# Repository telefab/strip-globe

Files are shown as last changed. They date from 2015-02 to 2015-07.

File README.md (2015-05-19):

LED strip-based, FPGA-powered POV globe
===

Documentation
---

Documentation is [available on Instructables](http://www.instructables.com/id/Globe-of-persistence-of-vision/).

Source structure
---

* `app_sources`: sources of programs running on the globe
* `board`: power board Eagle model
* `fpga_sources`: VHDL files for the FPGA
* `Solidworks`: model for the physical design
* `zybo_project`: integration on the Zybo board. The Vivado project references the `fpga_sources` files

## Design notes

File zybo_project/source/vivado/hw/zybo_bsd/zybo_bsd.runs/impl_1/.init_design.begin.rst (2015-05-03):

<?xml version="1.0"?>
<ProcessHandle Version="1" Minor="0">
    <Process Command=".planAhead." Owner="phhorrei" Host="" Pid="14742">
    </Process>
</ProcessHandle>

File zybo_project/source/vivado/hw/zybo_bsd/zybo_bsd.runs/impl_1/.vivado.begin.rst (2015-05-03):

<?xml version="1.0"?>
<ProcessHandle Version="1" Minor="0">
    <Process Command="vivado" Owner="phhorrei" Host="njord" Pid="14716">
    </Process>
</ProcessHandle>

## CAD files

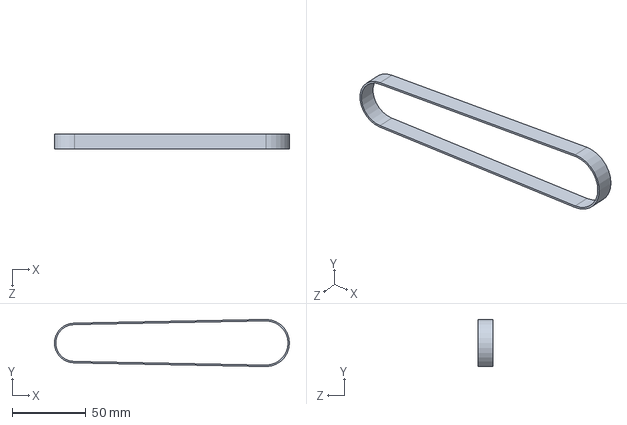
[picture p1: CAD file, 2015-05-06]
mechanics/courroie.SLDPRT
159.4 x 32.0 x 10.0 mm

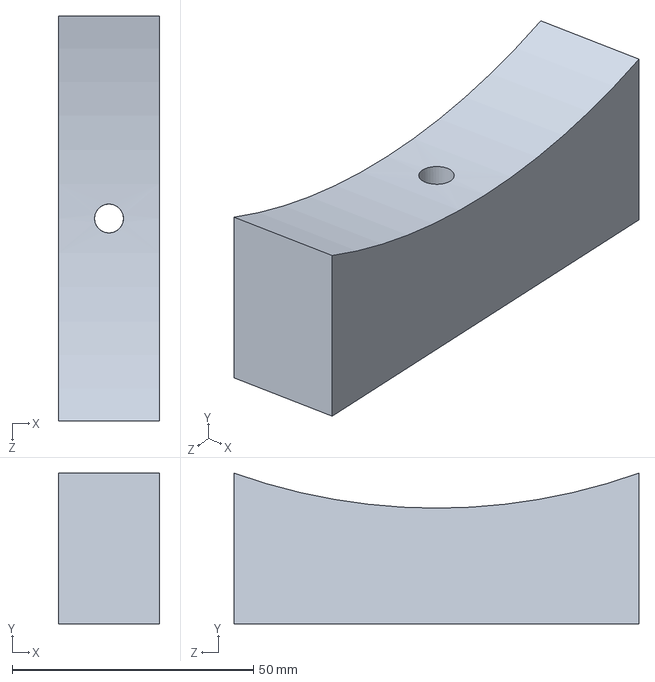
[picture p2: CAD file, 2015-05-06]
mechanics/Modélisation_anneau_fine/fixation_anneau.SLDPRT
21.0 x 31.3 x 84.0 mm

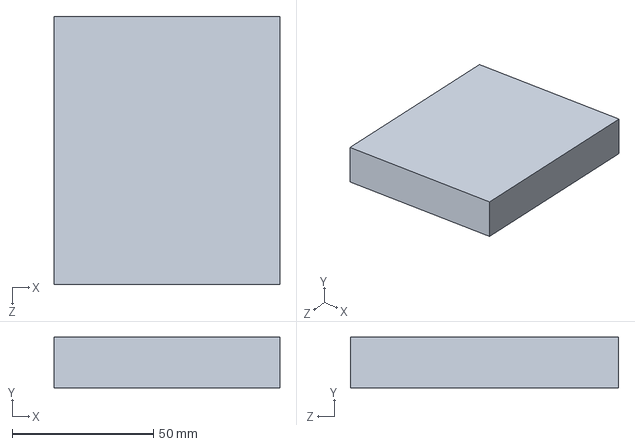
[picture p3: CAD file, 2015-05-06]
mechanics/Modélisation_structure_moteur/toit_structure.SLDPRT
80.0 x 18.0 x 95.0 mm

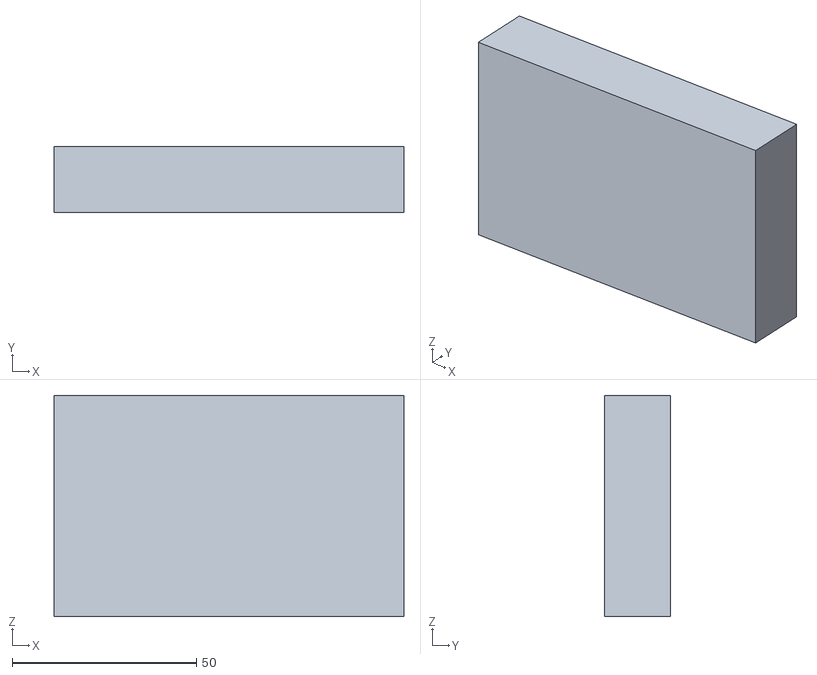
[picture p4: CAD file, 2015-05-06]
mechanics/STL/liaison_structure_moteur.STL
95.0 x 18.0 x 60.0

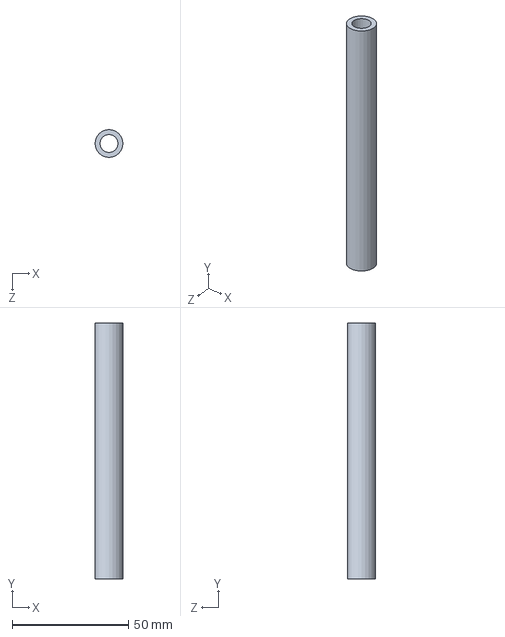
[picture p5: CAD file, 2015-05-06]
mechanics/axe_creux.SLDPRT
12.0 x 110.0 x 12.0 mm

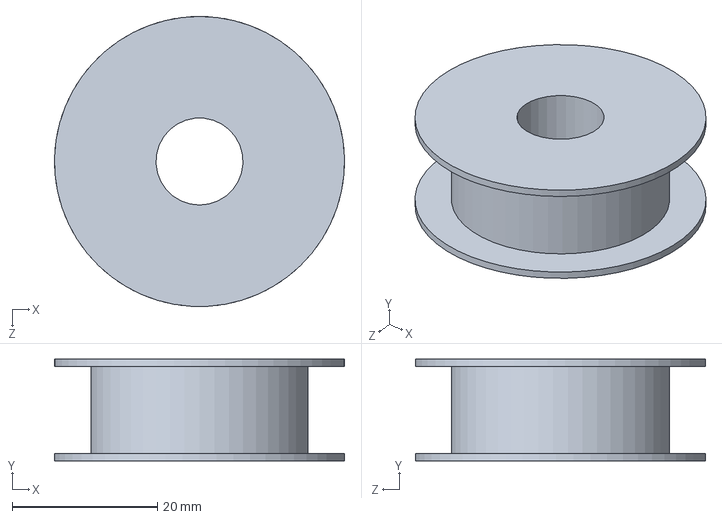
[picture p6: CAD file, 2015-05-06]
mechanics/Modélisation_anneau_fine/pignon_axe.SLDPRT
40.0 x 14.0 x 40.0 mm

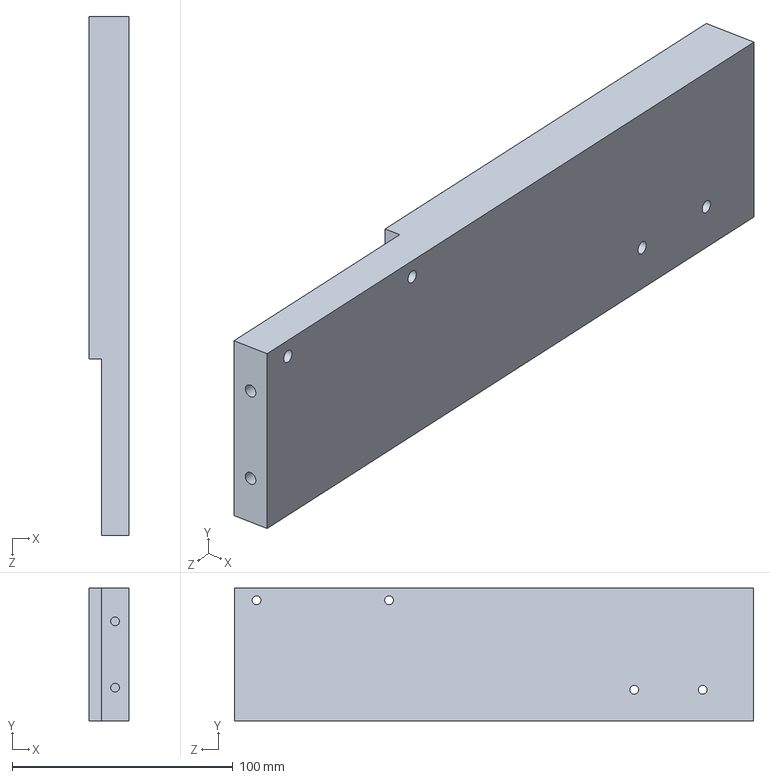
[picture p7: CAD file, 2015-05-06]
mechanics/Modélisation_structure_moteur/support_structure_moteur_sym.SLDPRT
18.0 x 60.0 x 235.0 mm

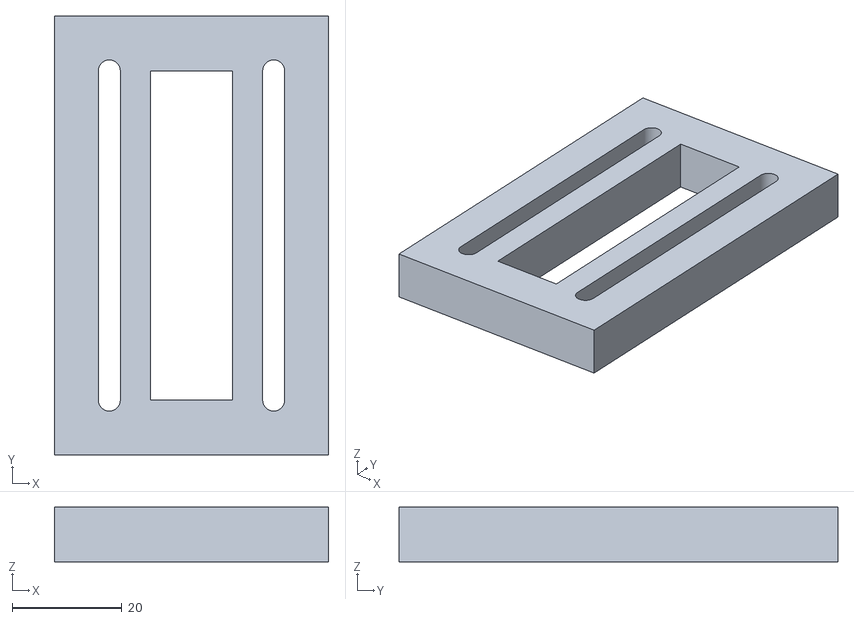
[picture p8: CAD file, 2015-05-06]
mechanics/STL/fixation_moteur_roof.STL
50.0 x 80.0 x 10.0

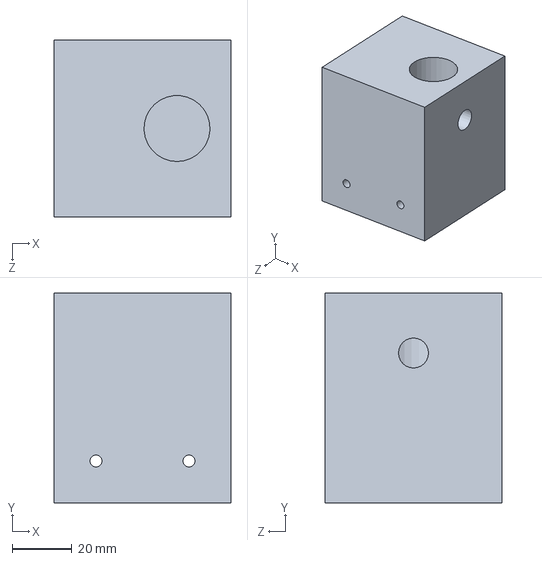
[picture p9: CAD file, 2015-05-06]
mechanics/Modélisation_anneau_fine/base.SLDPRT
59.0 x 70.0 x 59.0 mm

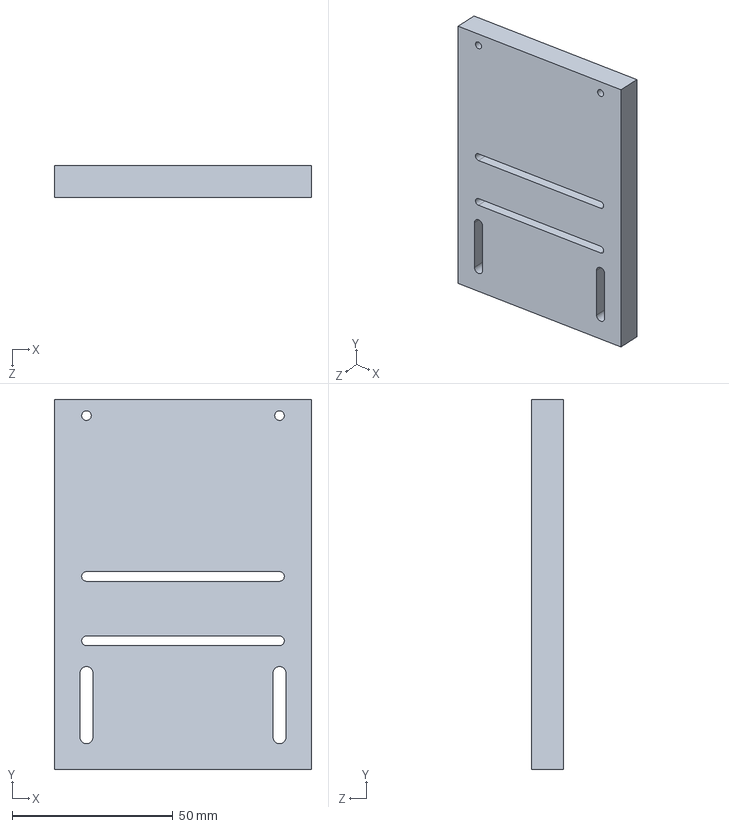
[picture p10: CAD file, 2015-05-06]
mechanics/Modélisation_structure_moteur/fixation_moteur_v2_side.SLDPRT
80.0 x 115.0 x 10.0 mm

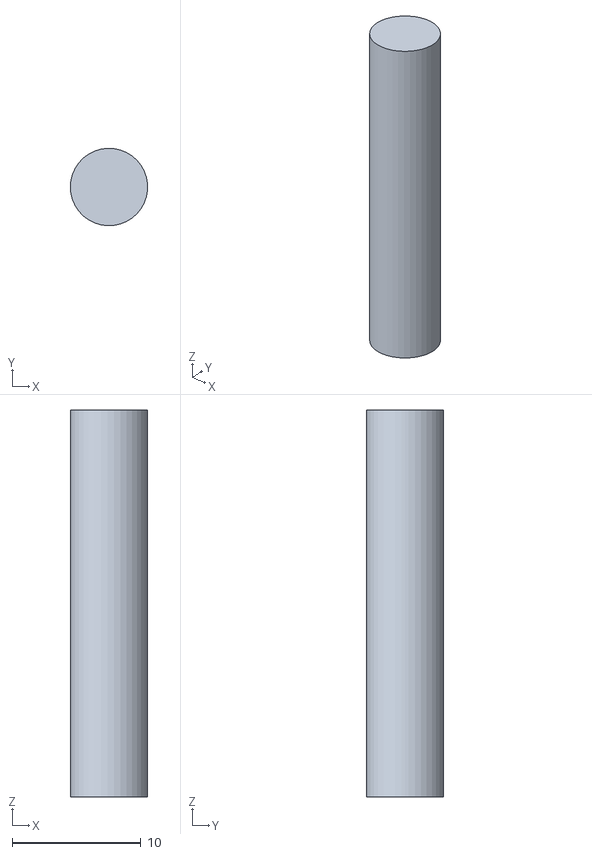
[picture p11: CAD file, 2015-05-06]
mechanics/STL/axe_soutien.STL
6.00 x 5.99 x 30.0

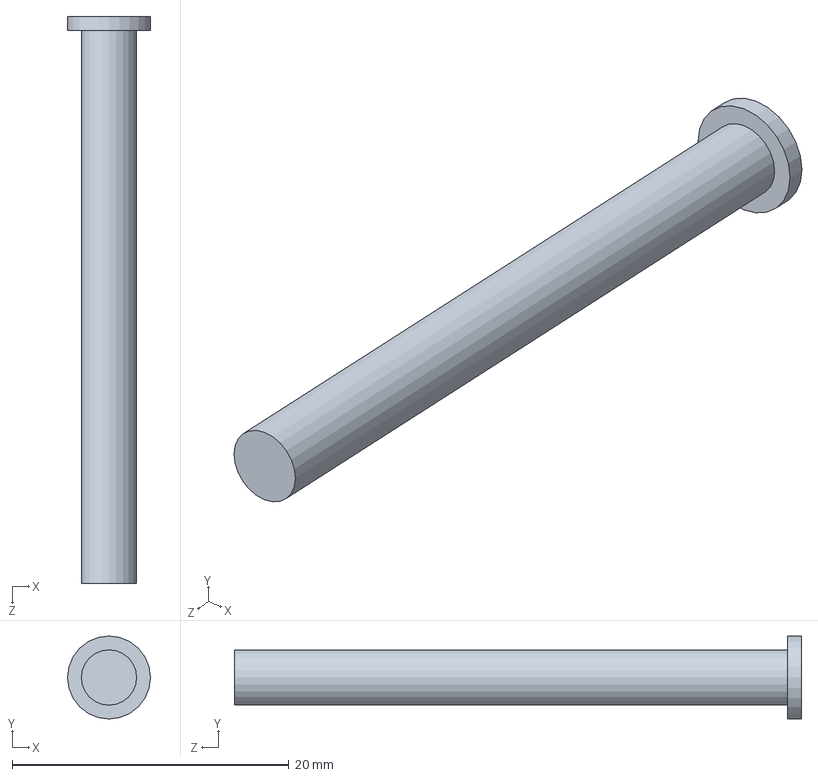
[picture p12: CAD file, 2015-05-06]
mechanics/vis_4.SLDPRT
6.00 x 6.00 x 41.0 mm

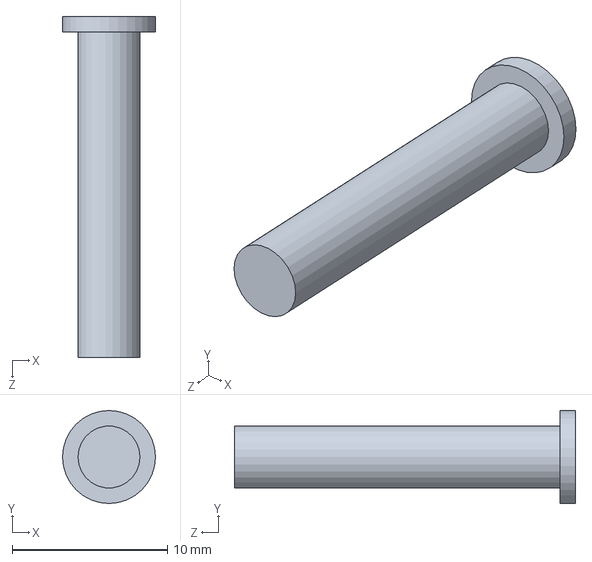
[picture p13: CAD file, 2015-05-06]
mechanics/mini_vis_4.SLDPRT
6.00 x 6.00 x 22.0 mm

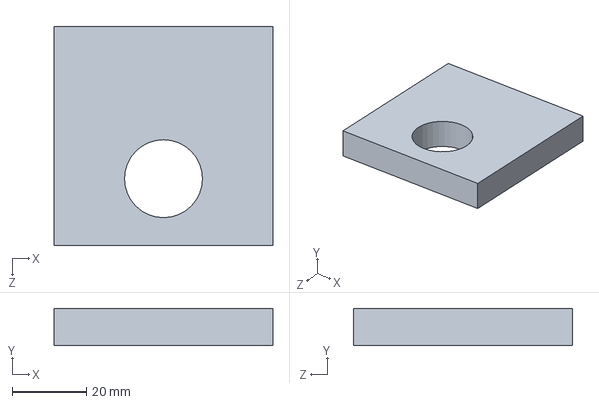
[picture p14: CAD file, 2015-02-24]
mechanics/Modélisation_anneau_fine/plaque.SLDPRT
59.0 x 10.0 x 59.0 mm

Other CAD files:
mechanics/Modélisation_structure_moteur/fixation_moteur_v2_roulement.SLDPRT
mechanics/STL/fixation_moteur_v2_side.STL
mechanics/Modélisation_anneau_fine/colonne.SLDPRT
mechanics/Modélisation_structure_moteur/fixation_moteur_roof.SLDPRT
mechanics/Modélisation_structure_moteur/axe_soutien.SLDPRT
mechanics/Modélisation_structure_moteur/fixation_moteur_v2.SLDPRT
mechanics/Modélisation_structure_moteur/liaison_structure_moteur.SLDPRT
mechanics/Modélisation_structure_moteur/moteur.SLDPRT
mechanics/Modélisation_structure_moteur/pignon_moteur_v2.SLDPRT
mechanics/Modélisation_structure_moteur/roulement_soutien_moteur.SLDPRT
mechanics/Modélisation_structure_moteur/support_globe.SLDPRT
mechanics/Modélisation_structure_moteur/support_structure_moteur.SLDPRT
mechanics/STL/anneau.STL
mechanics/STL/axe_creux.STL
mechanics/STL/base.STL
mechanics/STL/colonne.STL
mechanics/STL/fixation_anneau.STL
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

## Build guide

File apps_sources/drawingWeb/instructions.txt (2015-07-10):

// TODO: trouver un moyen de corriger définitivement les problèmes de permissions dans le dossier /var/www (devrait appartenir en entier à www-data) -> cause des 403 forbidden
// TODO 2: générer une clef rsa pour le serveur ssh. (http://www.softec.lu/site/DevelopersCorner/HowToRegenerateNewSsh ?)

1. Suivre l'instructable jusqu'à l'étape l'étape du buildroot:
  http://www.instructables.com/id/Globe-of-persistence-of-vision/step3/Installing-Linux-on-the-globe/

2. Installer lighttpd :
    make menuconfig
        target Package
                |
                ----> Networking Applications
                                |
                                -----> lighttpd
    sauvgarder/quitter
    
    make

3. Cross-compilation de node.js
    git clone 
    /!\ python doit être un lien vers python2
        Pour ceux dont ce n'est pas le cas -> ln -s /path/to/python2 python
                                              ln -s /path/to/python2-config python-config
                                              export PATH=`pwd`:$PATH
    export XILINX_TGT=arm-xilinx-linux-gnueabi
    export AR=$XILINX_TGT-ar
    export CC=$XILINX_TGT-gcc
    export CXX=$XILINX_TGT-g++
    export LINK=$XILINX_TGT-g++
    export PATH=$PATH:/path/to/xilinxToolchain/bin

    ./configure --without-snapshot --dest-cpu=arm --dest-os=linux

    make -j`nproc`
    make install DESTDIR=/dir/to/buildroot/output/target
    
    Copier libstdc+.so.6 du cross compilo dans /dir/to/buildroot/output/target/lib
    Personnelement j'ai trouvé libstdc++.so.6 dans
         /path/to/xilinxToolchain/libc/usr/lib/libstdc++.so.6

4. Compilation des modules node.js 
    avec les mêmes export que si dessus
            
    dans un répertoire choisi:
    pour chaque module :
        npm install nomDuModule --prefix=./ --target=arm

    mv node_modules /dir/to/buildroot/output/target/root

5. Finalistation
    dans le répertoire de buildroot :
    copier le contenu du dossier client dans le répertoire output/target/var/www
    copier le contenu du dossier server dans le répertoire output/target/root/sphereWeb-server
    make
    puis copier le output/images/rootfs.cpio.uboot sur la partition 1 de la microSD du globe et le renomer en uramdisk.image.gz

    Dans la partition 2 de la microSD:
        modifier le fichier load.sh pour démarrer le serveur nodejs et le logiciel du globe
        ajouter :

# Fix permissions on /var/www
chown www-data:www-data -R /var/www

## Start servers

cd /mnt
nohup /usr/local/bin/node /root/sphereWeb-server/server.js &
./drawing

    démonter la carte SD, rebooter le globe, tout devrait fonctionner

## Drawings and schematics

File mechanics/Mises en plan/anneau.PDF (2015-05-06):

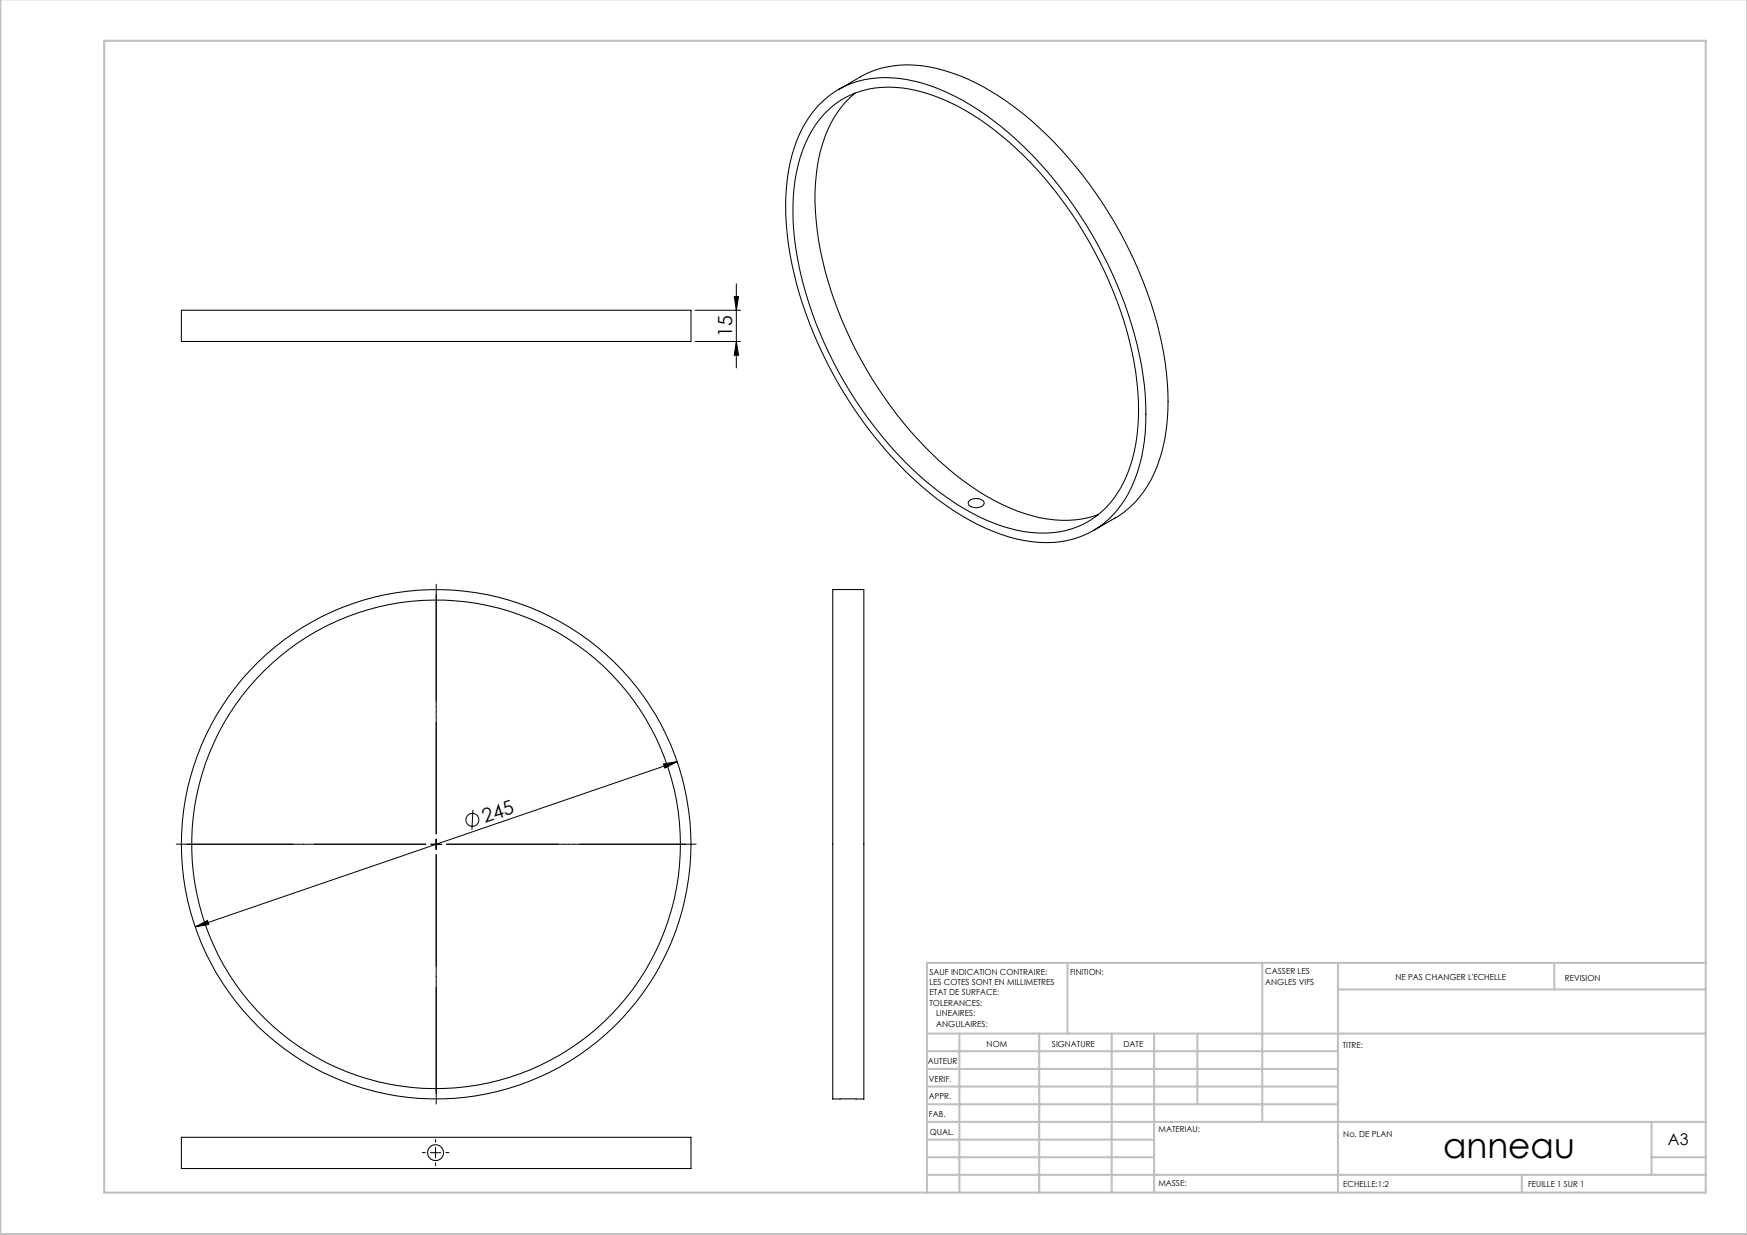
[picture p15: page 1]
ECHELLE:1:2; FEUILLE 1 SUR 1; NE PAS CHANGER L'ECHELLE; REVISION; CASSER LES ANGLES VIFS; SAUF INDICATION CONTRAIRE:; FINITION:

LES COTES SONT EN MILLIMETRES
ETAT DE SURFACE:
TOLERANCES:
LINEAIRES:
ANGULAIRES:

NOM | SIGNATURE | DATE | | | | TITRE:
QUAL. | | | | MATERIAU: | anneau MASSE: No. DE PLAN | A3

AUTEUR
VERIF.
APPR.
FAB.

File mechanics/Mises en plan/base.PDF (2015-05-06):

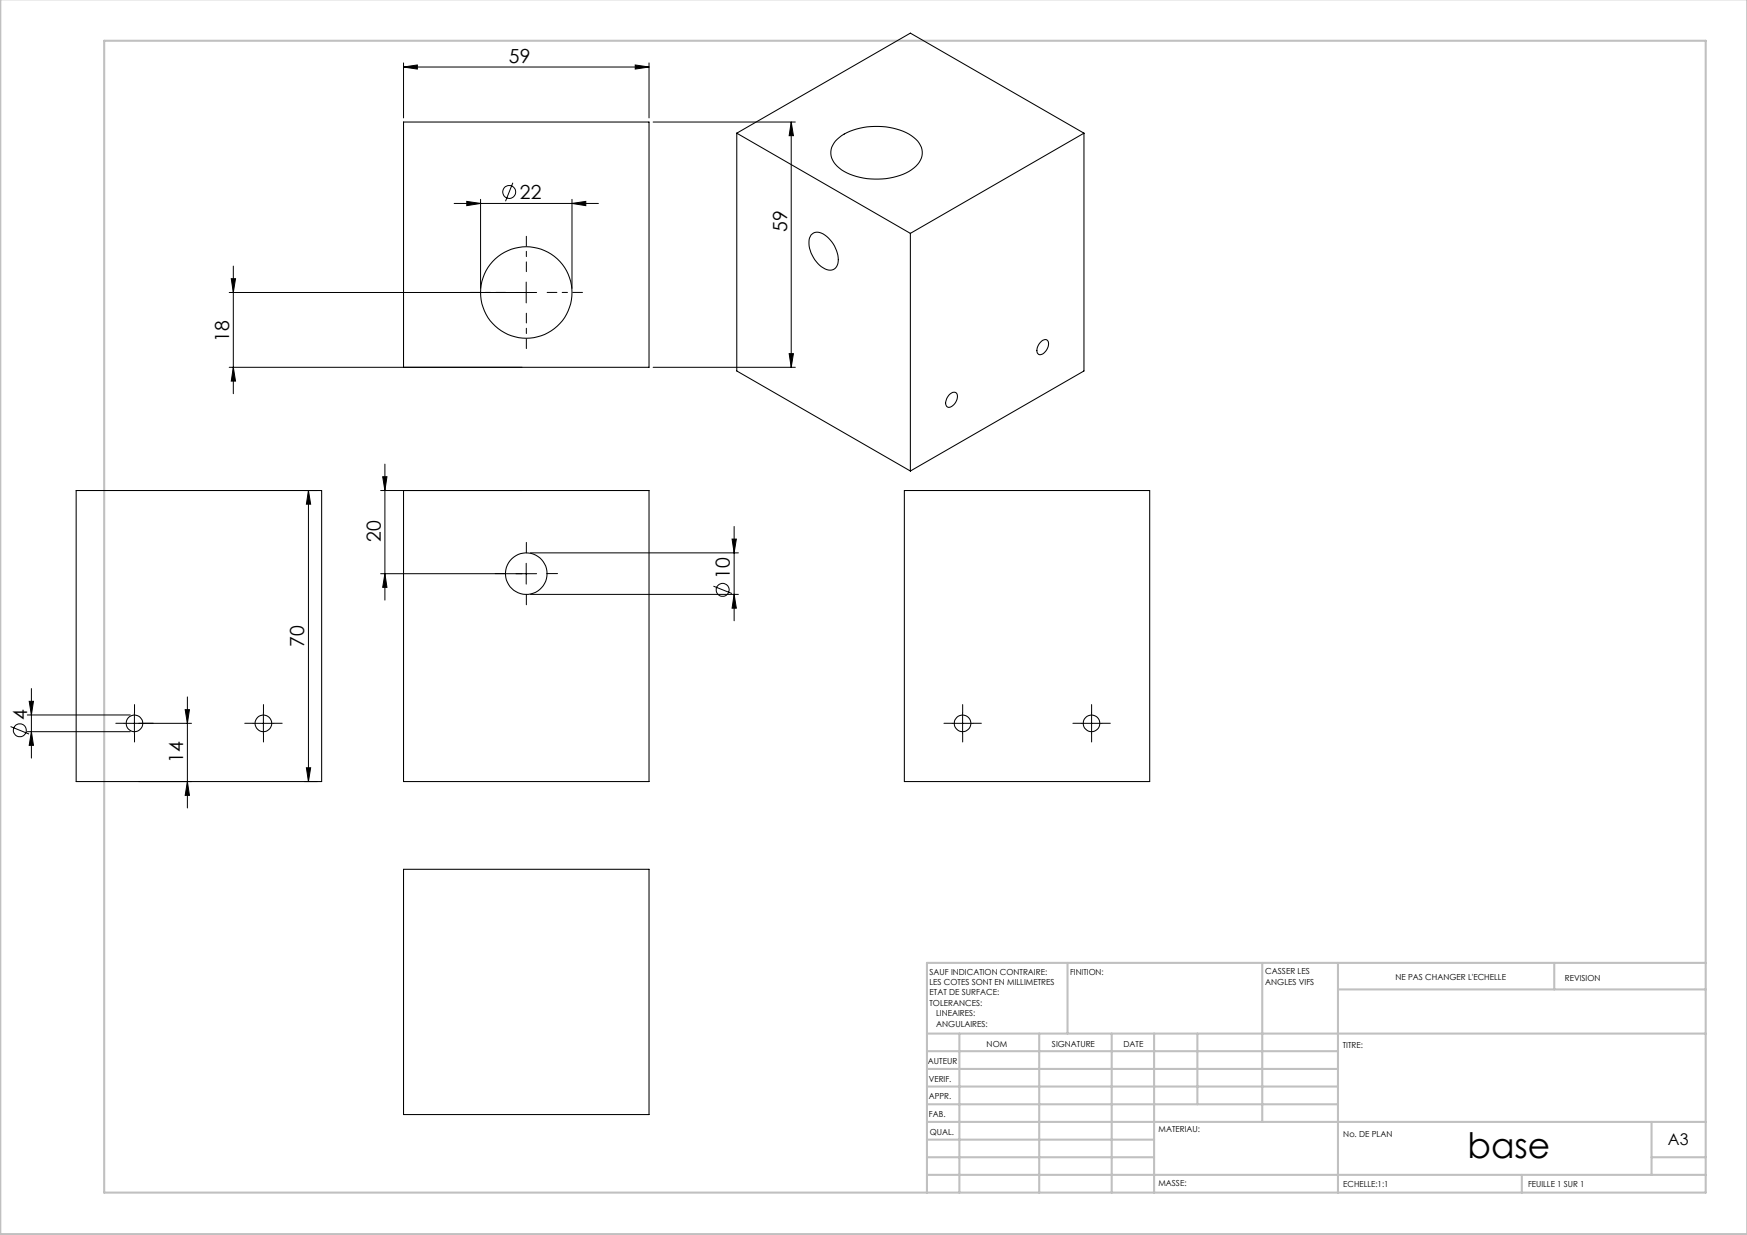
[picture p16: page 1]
ECHELLE:1:1; FEUILLE 1 SUR 1; NE PAS CHANGER L'ECHELLE; REVISION; CASSER LES ANGLES VIFS; SAUF INDICATION CONTRAIRE:; FINITION:

LES COTES SONT EN MILLIMETRES
ETAT DE SURFACE:
TOLERANCES:
LINEAIRES:
ANGULAIRES:

NOM | SIGNATURE | DATE | | | | TITRE:

AUTEUR
VERIF.
APPR.
FAB.
QUAL. | | | | MATERIAU: | base MASSE: No. DE PLAN | A3

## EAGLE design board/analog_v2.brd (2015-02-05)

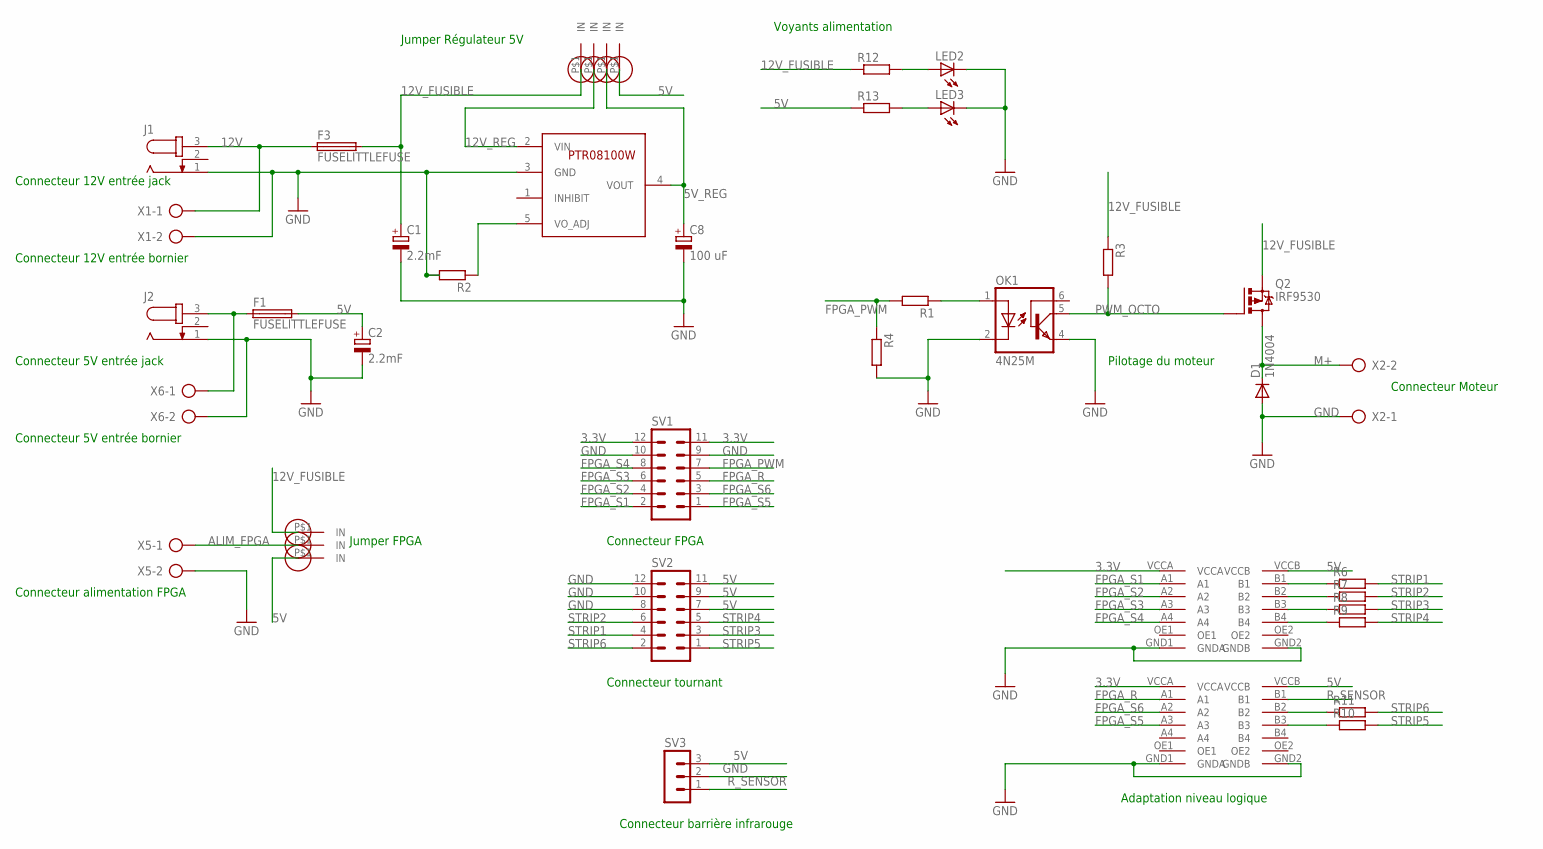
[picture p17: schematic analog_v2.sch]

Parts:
C1, C2: 2.2mF; E7,5-16
C8: 100 uF; E2,5-7
D1: 1N4004; DO41-10
F1, F3: FUSELITTLEFUSE; LITTLEFUSE
J1, J2: JACK-PLUG1; SPC4078
LED2, LED3: LED5MM
OK1: 4N25M; DIL06; MPN 4N25-M
Q2: IRF9530; TO220BV
R1, R2, R3, R4, R6, R7, R8, R9, R10, R11, R12, R13: R-EU_0207/10; 0207/10
SV1, SV2: MA06-2
SV3: MA03-1
U2: PTR08100W
U$1, U$2: TXB0104
U$3, U$4, U$5, U$6, U$7, U$10, U$12: JUMPER_CONNECTOR
X1, X2, X5, X6: AK500/2

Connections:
3.3V: SV1.11, SV1.12, U$1.VCCA, U$2.VCCA
5V: C2.+, F1.2, R13.1, SV2.7, SV2.9, SV2.11, SV3.3, U$1.VCCB, U$2.VCCB, U$5.P$1, U$10.P$1
5V_IN: F1.1, J2.3, X6.1
5V_REG: C8.+, U2.4 (VOUT), U$12.P$1
12V: F3.1, J1.3, X1.1
12V_FUSIBLE: C1.+, F3.2, Q2.S, R3.1, R12.1, U$3.P$1, U$6.P$1
12V_REG: U2.2 (VIN), U$7.P$1
ALIM_FPGA: U$4.P$1, X5.1
FPGA_PWM: R1.2, R4.1, SV1.7
FPGA_R: SV1.5, U$2.A1
FPGA_S1: SV1.2, U$1.A1
FPGA_S2: SV1.4, U$1.A2
FPGA_S3: SV1.6, U$1.A3
FPGA_S4: SV1.8, U$1.A4
FPGA_S5: SV1.1, U$2.A3
FPGA_S6: SV1.3, U$2.A2
GND: C1.-, C2.-, C8.-, D1.A, J1.1, J2.1, LED2.K (C), LED3.K (C), OK1.2 (C), OK1.4 (EMI), R2.2, R4.2, SV1.9, SV1.10, SV2.8, SV2.10, SV2.12, SV3.2, U2.3 (GND), U$1.GND1 (GNDA), U$1.GND2 (GNDB), U$2.GND1 (GNDA), U$2.GND2 (GNDB), X1.2, X2.1, X5.2, X6.2
M+: D1.C, Q2.D, X2.2
PWM_OCTO: OK1.5 (COL), Q2.G, R3.2
RES_LED_5V: LED3.A, R13.2
RES_LED_12V: LED2.A, R12.2
RES_OCTO: OK1.1 (A), R1.1
R_SENSOR: SV3.1, U$2.B1
R_STRIP_1: R6.1, U$1.B1
R_STRIP_2: R7.1, U$1.B2
R_STRIP_3: R8.1, U$1.B3
R_STRIP_4: R9.1, U$1.B4
R_STRIP_5: R10.1, U$2.B3
R_STRIP_6: R11.1, U$2.B2
STRIP1: R6.2, SV2.4
STRIP2: R7.2, SV2.6
STRIP3: R8.2, SV2.3
STRIP4: R9.2, SV2.5
STRIP5: R10.2, SV2.1
STRIP6: R11.2, SV2.2
VO_ADJ: R2.1, U2.5 (VO_ADJ)

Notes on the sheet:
Connecteur FPGA
Connecteur tournant
Connecteur barrière infrarouge
Connecteur Moteur
Connecteur 12V entrée jack
Jumper Régulateur 5V
Connecteur 5V entrée jack
Connecteur 12V entrée bornier
Connecteur alimentation FPGA
Voyants alimentation
Jumper FPGA
Connecteur 5V entrée bornier
Adaptation niveau logique
Pilotage du moteur

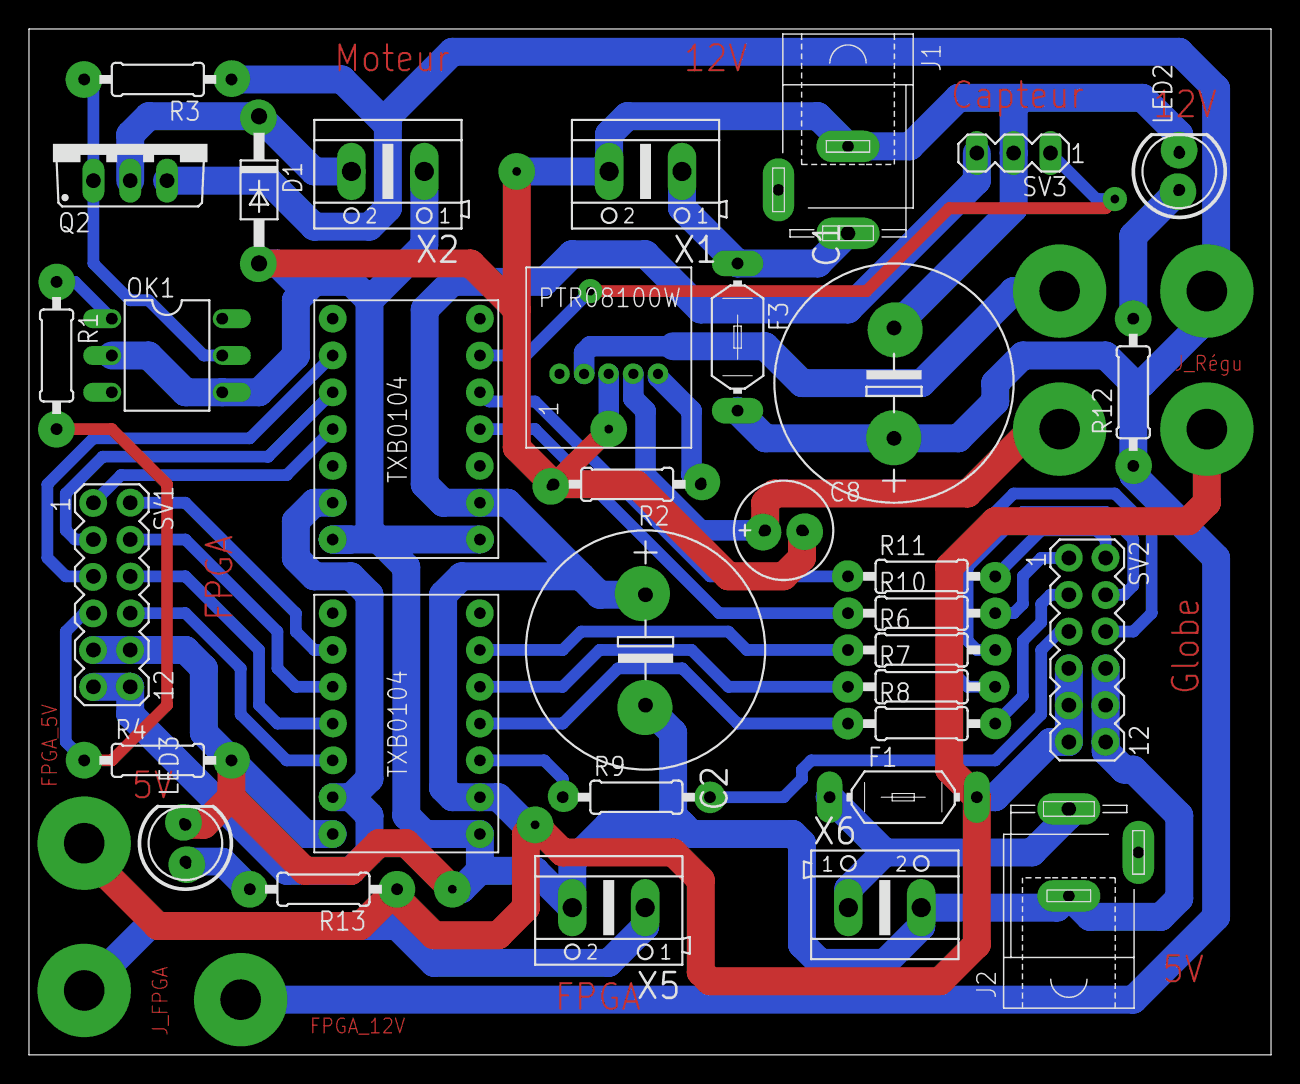
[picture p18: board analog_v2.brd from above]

Board: 2 copper layers, 85.7 x 70.8 mm, 41 parts (0 on the bottom side), 36 nets.

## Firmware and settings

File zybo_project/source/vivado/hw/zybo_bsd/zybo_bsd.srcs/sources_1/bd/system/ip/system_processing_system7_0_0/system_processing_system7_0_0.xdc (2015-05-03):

############################################################################
##
##  Xilinx, Inc. 2006            www.xilinx.com
############################################################################
##  File name :       ps7_constraints.xdc
##
##  Details :     Constraints file
##                    FPGA family:       zynq
##                    FPGA:              xc7z010clg400-1
##                    Device Size:        xc7z010
##                    Package:            clg400
##                    Speedgrade:         -1
##
##
############################################################################
############################################################################
############################################################################
# Clock constraints                                                        #
############################################################################
create_clock -name clk_fpga_1 -period "6.666" [get_pins "PS7_i/FCLKCLK[1]"]
set_input_jitter clk_fpga_1 0.19998
#The clocks are asynchronous, user should constrain them appropriately.#
create_clock -name clk_fpga_2 -period "81.538" [get_pins "PS7_i/FCLKCLK[2]"]
set_input_jitter clk_fpga_2 2.44614
#The clocks are asynchronous, user should constrain them appropriately.#
create_clock -name clk_fpga_0 -period "10" [get_pins "PS7_i/FCLKCLK[0]"]
set_input_jitter clk_fpga_0 0.3
#The clocks are asynchronous, user should constrain them appropriately.#


############################################################################
# I/O STANDARDS and Location Constraints                                   #
############################################################################

#  Enet 0 / mdio / MIO[53]
set_property iostandard "LVCMOS18" [get_ports "MIO[53]"]
set_property PACKAGE_PIN "C11" [get_ports "MIO[53]"]
set_property slew "slow" [get_ports "MIO[53]"]
set_property drive "8" [get_ports "MIO[53]"]
set_property PIO_DIRECTION "BIDIR" [get_ports "MIO[53]"]
#  Enet 0 / mdc / MIO[52]
set_property iostandard "LVCMOS18" [get_ports "MIO[52]"]
set_property PACKAGE_PIN "C10" [get_ports "MIO[52]"]
set_property slew "slow" [get_ports "MIO[52]"]
set_property drive "8" [get_ports "MIO[52]"]
set_property PIO_DIRECTION "OUTPUT" [get_ports "MIO[52]"]
#  UART 1 / rx / MIO[49]
set_property iostandard "LVCMOS18" [get_ports "MIO[49]"]
set_property PACKAGE_PIN "C12" [get_ports "MIO[49]"]
set_property slew "slow" [get_ports "MIO[49]"]
set_property drive "8" [get_ports "MIO[49]"]
set_property PIO_DIRECTION "INPUT" [get_ports "MIO[49]"]
#  UART 1 / tx / MIO[48]
set_property iostandard "LVCMOS18" [get_ports "MIO[48]"]
set_property PACKAGE_PIN "B12" [get_ports "MIO[48]"]
set_property slew "slow" [get_ports "MIO[48]"]
set_property drive "8" [get_ports "MIO[48]"]
set_property PIO_DIRECTION "OUTPUT" [get_ports "MIO[48]"]
#  SD 0 / cd / MIO[47]
set_property iostandard "LVCMOS18" [get_ports "MIO[47]"]
set_property PACKAGE_PIN "B14" [get_ports "MIO[47]"]
set_property slew "slow" [get_ports "MIO[47]"]
set_property drive "8" [get_ports "MIO[47]"]
set_property pullup "TRUE" [get_ports "MIO[47]"]
set_property PIO_DIRECTION "INPUT" [get_ports "MIO[47]"]
#  SD 0 / data[3] / MIO[45]
set_property iostandard "LVCMOS18" [get_ports "MIO[45]"]
set_property PACKAGE_PIN "B15" [get_ports "MIO[45]"]
set_property slew "fast" [get_ports "MIO[45]"]
set_property drive "8" [get_ports "MIO[45]"]
set_property PIO_DIRECTION "BIDIR" [get_ports "MIO[45]"]
#  SD 0 / data[2] / MIO[44]
set_property iostandard "LVCMOS18" [get_ports "MIO[44]"]
set_property PACKAGE_PIN "F13" [get_ports "MIO[44]"]
set_property slew "fast" [get_ports "MIO[44]"]
set_property drive "8" [get_ports "MIO[44]"]
set_property PIO_DIRECTION "BIDIR" [get_ports "MIO[44]"]
#  SD 0 / data[1] / MIO[43]
set_property iostandard "LVCMOS18" [get_ports "MIO[43]"]
set_property PACKAGE_PIN "A9" [get_ports "MIO[43]"]
set_property slew "fast" [get_ports "MIO[43]"]
set_property drive "8" [get_ports "MIO[43]"]
set_property PIO_DIRECTION "BIDIR" [get_ports "MIO[43]"]
#  SD 0 / data[0] / MIO[42]
set_property iostandard "LVCMOS18" [get_ports "MIO[42]"]
set_property PACKAGE_PIN "E12" [get_ports "MIO[42]"]
set_property slew "fast" [get_ports "MIO[42]"]
set_property drive "8" [get_ports "MIO[42]"]
set_property PIO_DIRECTION "BIDIR" [get_ports "MIO[42]"]
#  SD 0 / cmd / MIO[41]
set_property iostandard "LVCMOS18" [get_ports "MIO[41]"]
set_property PACKAGE_PIN "C17" [get_ports "MIO[41]"]
set_property slew "fast" [get_ports "MIO[41]"]
set_property drive "8" [get_ports "MIO[41]"]
set_property PIO_DIRECTION "BIDIR" [get_ports "MIO[41]"]
#  SD 0 / clk / MIO[40]
set_property iostandard "LVCMOS18" [get_ports "MIO[40]"]
set_property PACKAGE_PIN "D14" [get_ports "MIO[40]"]
set_property slew "fast" [get_ports "MIO[40]"]
set_property drive "8" [get_ports "MIO[40]"]
set_property PIO_DIRECTION "BIDIR" [get_ports "MIO[40]"]
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

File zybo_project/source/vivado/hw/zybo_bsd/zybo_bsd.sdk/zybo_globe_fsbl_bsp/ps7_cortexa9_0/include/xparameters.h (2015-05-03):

/* Definition for CPU ID */
#define XPAR_CPU_ID 0

/* Definitions for peripheral PS7_CORTEXA9_0 */
#define XPAR_PS7_CORTEXA9_0_CPU_CLK_FREQ_HZ 650000000


/******************************************************************/

/* Canonical definitions for peripheral PS7_CORTEXA9_0 */
#define XPAR_CPU_CORTEXA9_0_CPU_CLK_FREQ_HZ 650000000


/******************************************************************/

#include "xparameters_ps.h"

#define STDIN_BASEADDRESS 0xE0001000
#define STDOUT_BASEADDRESS 0xE0001000

/******************************************************************/

/* Definitions for driver DEVCFG */
#define XPAR_XDCFG_NUM_INSTANCES 1

/* Definitions for peripheral PS7_DEV_CFG_0 */
#define XPAR_PS7_DEV_CFG_0_DEVICE_ID 0
#define XPAR_PS7_DEV_CFG_0_BASEADDR 0xF8007000
#define XPAR_PS7_DEV_CFG_0_HIGHADDR 0xF80070FF


/******************************************************************/

/* Canonical definitions for peripheral PS7_DEV_CFG_0 */
#define XPAR_XDCFG_0_DEVICE_ID XPAR_PS7_DEV_CFG_0_DEVICE_ID
#define XPAR_XDCFG_0_BASEADDR 0xF8007000
#define XPAR_XDCFG_0_HIGHADDR 0xF80070FF


/******************************************************************/

/* Definitions for driver DMAPS */
#define XPAR_XDMAPS_NUM_INSTANCES 2

/* Definitions for peripheral PS7_DMA_NS */
#define XPAR_PS7_DMA_NS_DEVICE_ID 0
#define XPAR_PS7_DMA_NS_BASEADDR 0xF8004000
#define XPAR_PS7_DMA_NS_HIGHADDR 0xF8004FFF


/* Definitions for peripheral PS7_DMA_S */
#define XPAR_PS7_DMA_S_DEVICE_ID 1
#define XPAR_PS7_DMA_S_BASEADDR 0xF8003000
#define XPAR_PS7_DMA_S_HIGHADDR 0xF8003FFF


/******************************************************************/

/* Canonical definitions for peripheral PS7_DMA_NS */
#define XPAR_XDMAPS_0_DEVICE_ID XPAR_PS7_DMA_NS_DEVICE_ID
#define XPAR_XDMAPS_0_BASEADDR 0xF8004000
#define XPAR_XDMAPS_0_HIGHADDR 0xF8004FFF

/* Canonical definitions for peripheral PS7_DMA_S */
#define XPAR_XDMAPS_1_DEVICE_ID XPAR_PS7_DMA_S_DEVICE_ID
#define XPAR_XDMAPS_1_BASEADDR 0xF8003000
#define XPAR_XDMAPS_1_HIGHADDR 0xF8003FFF


/******************************************************************/

/* Definitions for driver EMACPS */
#define XPAR_XEMACPS_NUM_INSTANCES 1

/* Definitions for peripheral PS7_ETHERNET_0 */
#define XPAR_PS7_ETHERNET_0_DEVICE_ID 0
#define XPAR_PS7_ETHERNET_0_BASEADDR 0xE000B000
#define XPAR_PS7_ETHERNET_0_HIGHADDR 0xE000BFFF
#define XPAR_PS7_ETHERNET_0_ENET_CLK_FREQ_HZ 125000000
#define XPAR_PS7_ETHERNET_0_ENET_SLCR_1000MBPS_DIV0 8
#define XPAR_PS7_ETHERNET_0_ENET_SLCR_1000MBPS_DIV1 1
#define XPAR_PS7_ETHERNET_0_ENET_SLCR_100MBPS_DIV0 8
#define XPAR_PS7_ETHERNET_0_ENET_SLCR_100MBPS_DIV1 5
#define XPAR_PS7_ETHERNET_0_ENET_SLCR_10MBPS_DIV0 8
#define XPAR_PS7_ETHERNET_0_ENET_SLCR_10MBPS_DIV1 50


/******************************************************************/

/* Canonical definitions for peripheral PS7_ETHERNET_0 */
#define XPAR_XEMACPS_0_DEVICE_ID XPAR_PS7_ETHERNET_0_DEVICE_ID
#define XPAR_XEMACPS_0_BASEADDR 0xE000B000
#define XPAR_XEMACPS_0_HIGHADDR 0xE000BFFF
#define XPAR_XEMACPS_0_ENET_CLK_FREQ_HZ 125000000
#define XPAR_XEMACPS_0_ENET_SLCR_1000Mbps_DIV0 8
#define XPAR_XEMACPS_0_ENET_SLCR_1000Mbps_DIV1 1
#define XPAR_XEMACPS_0_ENET_SLCR_100Mbps_DIV0 8
#define XPAR_XEMACPS_0_ENET_SLCR_100Mbps_DIV1 5
#define XPAR_XEMACPS_0_ENET_SLCR_10Mbps_DIV0 8
#define XPAR_XEMACPS_0_ENET_SLCR_10Mbps_DIV1 50


/******************************************************************/


/* Definitions for peripheral PS7_AFI_0 */
#define XPAR_PS7_AFI_0_S_AXI_BASEADDR 0xF8008000
#define XPAR_PS7_AFI_0_S_AXI_HIGHADDR 0xF8008FFF


/* Definitions for peripheral PS7_AFI_1 */
#define XPAR_PS7_AFI_1_S_AXI_BASEADDR 0xF8009000
#define XPAR_PS7_AFI_1_S_AXI_HIGHADDR 0xF8009FFF


/* Definitions for peripheral PS7_AFI_2 */
#define XPAR_PS7_AFI_2_S_AXI_BASEADDR 0xF800A000
#define XPAR_PS7_AFI_2_S_AXI_HIGHADDR 0xF800AFFF


/* Definitions for peripheral PS7_AFI_3 */
#define XPAR_PS7_AFI_3_S_AXI_BASEADDR 0xF800B000
#define XPAR_PS7_AFI_3_S_AXI_HIGHADDR 0xF800BFFF


/* Definitions for peripheral PS7_CORESIGHT_COMP_0 */
#define XPAR_PS7_CORESIGHT_COMP_0_S_AXI_BASEADDR 0xF8800000
#define XPAR_PS7_CORESIGHT_COMP_0_S_AXI_HIGHADDR 0xF88FFFFF


/* Definitions for peripheral PS7_DDR_0 */
#define XPAR_PS7_DDR_0_S_AXI_BASEADDR 0x00100000
#define XPAR_PS7_DDR_0_S_AXI_HIGHADDR 0x1FFFFFFF


/* Definitions for peripheral PS7_DDRC_0 */
#define XPAR_PS7_DDRC_0_S_AXI_BASEADDR 0xF8006000
#define XPAR_PS7_DDRC_0_S_AXI_HIGHADDR 0xF8006FFF


/* Definitions for peripheral PS7_GLOBALTIMER_0 */
#define XPAR_PS7_GLOBALTIMER_0_S_AXI_BASEADDR 0xF8F00200
#define XPAR_PS7_GLOBALTIMER_0_S_AXI_HIGHADDR 0xF8F002FF


/* Definitions for peripheral PS7_GPV_0 */
#define XPAR_PS7_GPV_0_S_AXI_BASEADDR 0xF8900000
#define XPAR_PS7_GPV_0_S_AXI_HIGHADDR 0xF89FFFFF


/* Definitions for peripheral PS7_INTC_DIST_0 */
#define XPAR_PS7_INTC_DIST_0_S_AXI_BASEADDR 0xF8F01000
#define XPAR_PS7_INTC_DIST_0_S_AXI_HIGHADDR 0xF8F01FFF
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

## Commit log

2014-11-24 Version 0.0 This commit only contains the motor controller
    [a_0319736121_2372691052.nt64.obj, a_1391599013_3212880686.nt64.obj, a_4194632468_3212880686.nt64.obj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]
2014-11-25 Version 0.2 Ajout de la carte d'extension pour le globe
    [analog.brd, analog.sch]
2014-11-27 Projet Globe Version 0.3 Fichier de test pour allumer les leds en bleu, blanc et rouge.
2014-12-02 Projet S5 Globe Version 0.5 Nouvelle version de la carte d'extension du FPGA
    [analog_v2.brd, analog_v2.sch]
2015-02-05 Projet Globe V0.5 Synchro added
    [analog.brd]
2015-02-08 Globe working for the zybo board
2015-02-13 globe fonctionnant avec la synchro et les deux frame buffer + le .bit
2015-02-24 Projet S5 Globe V2.5 Ajout des fichiers solidworks et des drivers moteurs
    [anneau.SLDPRT, axe_creux.SLDPRT, barrière_infra.SLDPRT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]
2015-04-07 Sources VHDL de L'IP
2015-05-03 Cleaned up sources, added new strip code.
    This code has been used successfuly at Maker Faire St Malo
    It requires a double check, to be done soon.
    [a_0319736121_2372691052.nt64.obj, a_1391599013_3212880686.nt64.obj, a_4194632468_3212880686.nt64.obj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]
2015-05-06 Project: Globe of persistence of vision
    Adds the applications and drivers sources, the solidworks modelisations
    and the config files for setting up the Linux
    [anneau.SLDPRT, anneau.STL, axe_creux.SLDPRT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]
2015-05-10 The globe of persistence of vision
    The application sources have been corrected and adapted to the new globe
    [anneau.SLDPRT, axe_creux.SLDPRT, barrière_infra.SLDPRT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]
2015-05-10 The globe of persistence of vision
    Addresses of the devices modified to correspond to the new globes' ones
2015-07-10 Ajout du support de l'internationalisation
